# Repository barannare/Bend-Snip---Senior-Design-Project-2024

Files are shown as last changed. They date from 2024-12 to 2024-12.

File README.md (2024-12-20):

# Bend-Snip---Senior-Design-Project-2024
This is the Github Repository for the Tufts University 2024 Mechanical Engineering Senior Design Project - Bend &amp; Snip: The Automated Jumper Wire Cutter. This Project was completed by Elizabeth Abboud, ReAnna Barclay, Emma Gonzalez, and Kaitlin Necakov. The final code and all design materials for this project will be availbale here, as open source.  _Note: The Generative AI, ChatGPT, was used when creating the code for this project to help with syntax and debugging purposes._
AssemblyFinal-3

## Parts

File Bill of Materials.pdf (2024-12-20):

## Bill of Materials

Product: Bend & Snip, Automated Jumper Wire Cutter

Date: Dec 20, 2024

Assembly: Full Machine Assembly

Item # | Part # | Qty | Name | Material | Source | Cost (per unit)
1 | B0D1KQZHKL | 2 | Threaded Rod Lead Screw | 304 Stainless Steel | Amazon | $4.50
2 | B0D1KQZHKL | 2 | Lead Screw Nut | 304 Stainless Steel | Amazon | Included with Item #1
3 | B08ZJ854Z6 | 2 | 5 mm to 8 mm Shaft Coupling | Aluminum Alloy | Amazon | $4.27
4 | B00161GBDW | 2 | Knipex Replacement Blade | Alloy Steel | Amazon | $10.74
5 | B09K1CNP6L | 1 | Boden Dual Gear Extruder | Stainless Steel | Amazon | $47.50
6 | B08ZK8BTNN | 1 | 3D Printer Tube | PTFE | Amazon | $8.99
7 | 1528-1743-ND | 5 | Hook-Up 22 AWG Solid Wire | Copper, PVC | Digikey | $3.19
8 | 1528-1743-ND | 1 | Wooden Dowel Rod | Wood | Digikey | Included with Item #7
9 | 9 | 2, 16.33 g each | Spool Holder Mount | Dual Color PLA | Amazon, Bambu Lab X1C | $0.41

10 | 10 | 1, 38.74 g | Extruder Motor Mount | Dual Color PLA | Amazon, Bambu Lab X1C | $0.98
11 | 11 | 1, 2.77 g | Extruder Motor Knob | Dual Color PLA | Amazon, Bambu Lab X1C | $0.07
12 | 12 | 1, 59.76 g | Bottom Blade Motor Mount | Dual Color PLA | Amazon, Bambu Lab X1C | $1.52
13 | 13 | 1, 12.70 g | Top Blade Mount | Dual Color PLA | Amazon, Bambu Lab X1C | $0.32
14 | 14 | 1, 4.48 g | Lead Screws Holder | Dual Color PLA | Amazon, Bambu Lab X1C | $0.11
15 | 15 | 1, 38.98 g | Bender Motor Mount | Dual Color PLA | Amazon, Bambu Lab X1C | $0.99
16 | 16 | 1, 4.56 g | Bender Arm | Dual Color PLA | Amazon, Bambu Lab X1C | $0.12
17 | 17 | 1, 42.23 g | Slide | Dual Color PLA | Amazon, Bambu Lab X1C | $1.10
18 | 18 | 1, 16.14 g | Bucket | Dual Color PLA | Amazon, Bambu Lab X1C | $0.41
19 | B0046AMGW0 | 1 | Arduino Mega 2560 | Fiberglass, Copper, Semicondu ctors | Amazon | $48.35
20 | 1528-1062-ND | 4 | Nema 17 Stepper Motor | Steel, Copper, Magnets | Digikey | $14.00
21 | B0C5JCF5RS | 3 | L298N Motor Driver | Fiberglass, Copper, Semicondu ctors | Amazon | $2.50

22 | ECPB_M_Multi_ 6P | 2 | Prototype Board Solderable Breadboard | Fiberglass, Copper | Amazon | $1.17
23 | B0B2L66ZFM | 8 | Breadboard Jumper Wires | Copper Clad Aluminum, PVC | Amazon | $0.06
24 | B019K5X53O | 1 | LCD Display Module | Liquid Crystals, Fiberglass, Copper, Semicondu ctors | Amazon | $9.99
25 | B00P7QBGD2 | 1 | Joystick Sensor | Plastic, Fiberglass, Copper, Semicondu ctors | Amazon | $6.99
26 | B072R1H185 | 2 | Arcade Button | Plastic, Fiberglass, Copper, Semicondu ctors | Amazon | $1.36
27 | 27 | 1 | Electronics Mounting Plate | Matte Black Acrylic | Makerstock, Universal VLS 3.60 | $7.75
28 | 28 | 1 | Front Screen Panel | Matte Black Acrylic | Makerstock, Universal VLS 3.60 | $7.75
29 | 29 | 1 | Side Port Panel | Matte Black Acrylic | Makerstock, Universal VLS 3.60 | $7.75
30 | 30 | 1 | Divider Panel | Matte Black Acrylic | Makerstock, Universal VLS 3.60 | $7.75
31 | 31 | 1 | Back Vent Panel | Matte Black Acrylic | Makerstock, Universal VLS 3.60 | $7.75

32 | 32 | 2 | Front/Back Enclosure Panel | Clear Acrylic | Makerstock, Universal VLS 3.60 | $4.48
33 | 33 | 2 | Sides Enclosure Panel | Clear Acrylic | Makerstock, Universal VLS 3.60 | $4.48
34 | 34 | 1 | Top Enclosure Panel | Clear Acrylic | Makerstock, Universal VLS 3.60 | $8.95
35 | B0BSDNPTL8 | 4 | Acrylic Corner Brackets | Clear Acrylic | Amazon | $1.28
36 | B0BSDNPTL8 | 12 | Acrylic Corner Bracket Bolts | Clear Acrylic | Amazon | Included with Item #35
37 | B0BSDNPTL8 | 12 | Acrylic Corner Bracket Nuts | Clear Acrylic | Amazon | Included with Item #35
38 | 38 | 4 | Aluminum Extrusion 315.6 mm | Silver Anodized Aluminum | McMaster-Carr | $2.84
39 | 39 | 4 | Aluminum Extrusion 177.8 mm | Silver Anodized Aluminum | McMaster-Carr | $2.84
40 | 40 | 4 | Aluminum Extrusion 101.6 mm | Silver Anodized Aluminum | McMaster-Carr | $2.84
41 | B0855V2JV3 | 20 | Aluminum Extrusion Corner Bracket | Aluminum | Amazon | $0.95
43 | 3136N409 | 55 | M5 x 0.8 mm 10 mm Long Socket Button Head Bolt | Zinc-Plated Steel | McMaster-Carr | $0.77
44 | 3136N409 | 55 | M5 x 0.8 mm Aluminum Extrusion Nut | Zinc-Plated Steel | McMaster-Carr | $0.77
45 | 91290A124 | 8 | M3 x 0.5 mm 22 mm Long | Black Oxide Class | McMaster-Carr | $0.13

| | | Socket Head Cap Bolt | 12.9 Alloy Steel
46 | 91290A119 | 2 | M3 x 0.5 mm 14 mm Long Socket Head CapBolt | Black Oxide Class 12.9 Alloy Steel | McMaster-Carr | $0.15
47 | 91290A115 | 44 | M3 x 0.5 mm 10 mm Long Socket Head Cap Bolt | Black Oxide Class 12.9 Alloy Steel | McMaster-Carr | $0.13
48 | 91290A109 | 12 | M3 x 0.5 mm 4 mm Long Socket HeadCap Bolt | Black Oxide Class 12.9 Alloy Steel | McMaster-Carr | $0.13
49 | 90591A250 | 66 | M3 x 0.5 mm Hex Nut | Zinc-Plated Steel | McMaster-Carr | $0.03
50 | 91290A049 | 4 | M2 x 0.4 mm 20 mm Long Socket Head Bolt | Black Oxide Class 12.9 Alloy Steel | McMaster-Carr | $0.15
51 | 90128A181 | 4 | M2 x 0.4 mm 10 mm Long Socket Head Cap Bolt | Zinc-Plated Class 12.9 Alloy Steel | McMaster-Carr | $0.13
52 | 90128A179 | 9 | M2 x 0.4 mm 8 mm Long Socket Head Cap Bolt | Zinc-Plated Class 12.9 Alloy Steel | McMaster-Carr | $0.13
53 | 09591A265 | 17 | M2 Hex Nut | Zinc-Plated Steel | McMaster-Carr | $0.02
54 | 54 | 1 | Assembly Mounting Plate | Matte Black Acrylic | Makerstock, Universal VLS 3.60 | $7.75
55 | B07DC5VFZ7 | 2 | 10 mm LED | Copper, Semicondu ctors | Amazon | $0.40
56 | B0C8141GB1 | 2 | L Bracket | Stainless Steel | Amazon | $0.15

Team Member | Prepared by: Kaitlin Necakov
Team Member | Checked by: ReAnna Barclay
Team Member | Approved by: Elizabeth Abboud

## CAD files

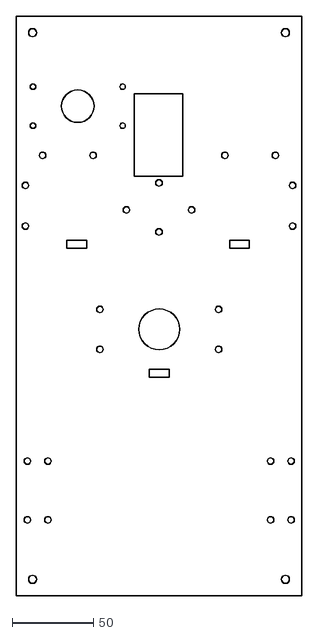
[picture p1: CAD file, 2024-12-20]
DXF Files/Assembly Mounting Plate.dxf
175.3 x 355.6

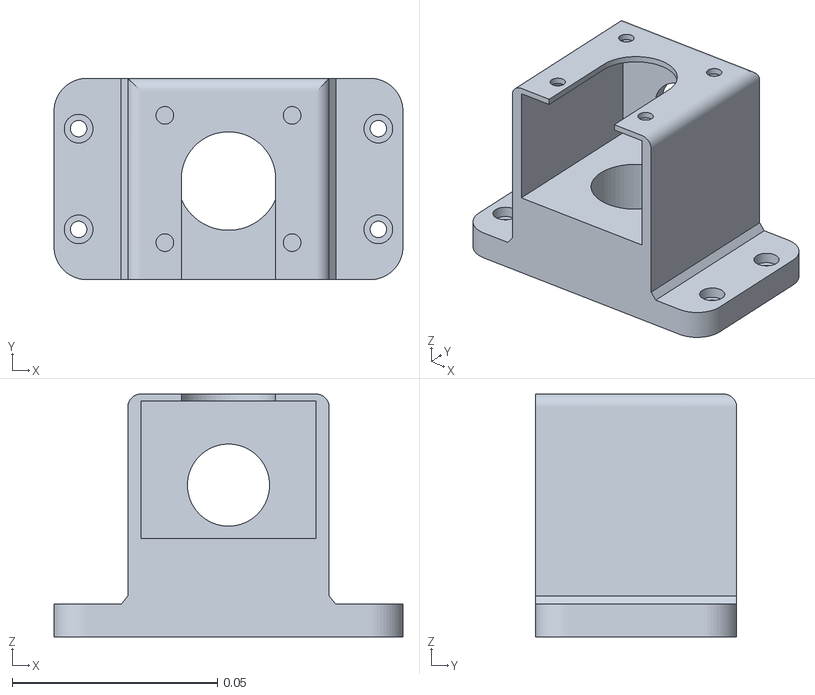
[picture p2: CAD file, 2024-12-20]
3D Print STL Files/Extruder Motor Mount.stl
0.085 x 0.049 x 0.0592

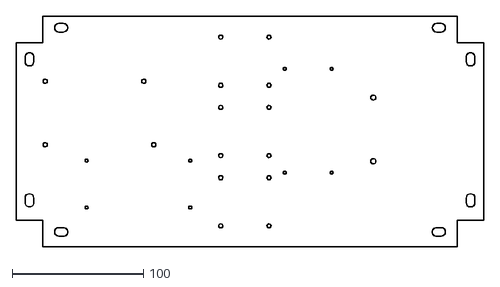
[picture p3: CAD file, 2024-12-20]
DXF Files/Electronics Mounting Plate.dxf
355.6 x 175.3

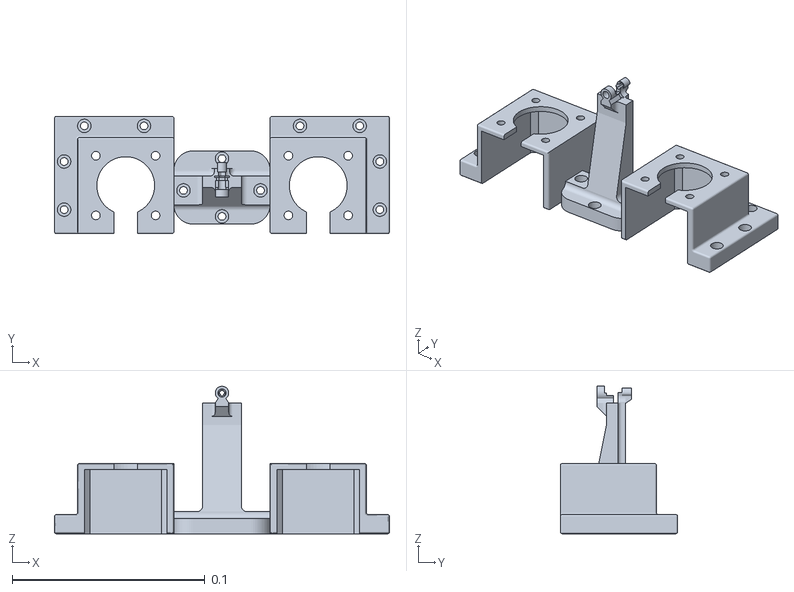
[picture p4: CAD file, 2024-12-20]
3D Print STL Files/Bottom Blade Motor Mount.stl
0.174 x 0.061 x 0.0766

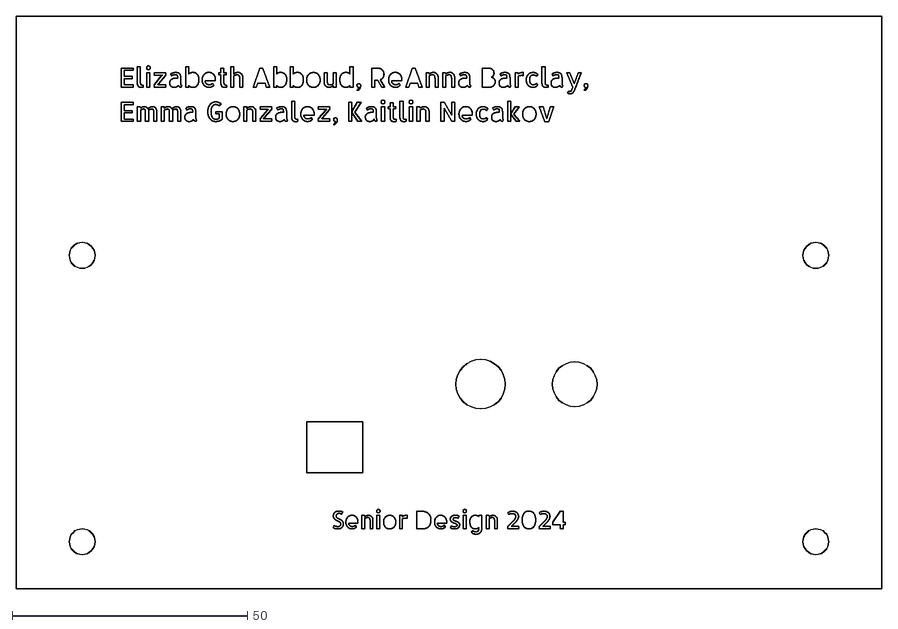
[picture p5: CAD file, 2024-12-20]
DXF Files/Side Port Panel.dxf
183.8 x 121.6

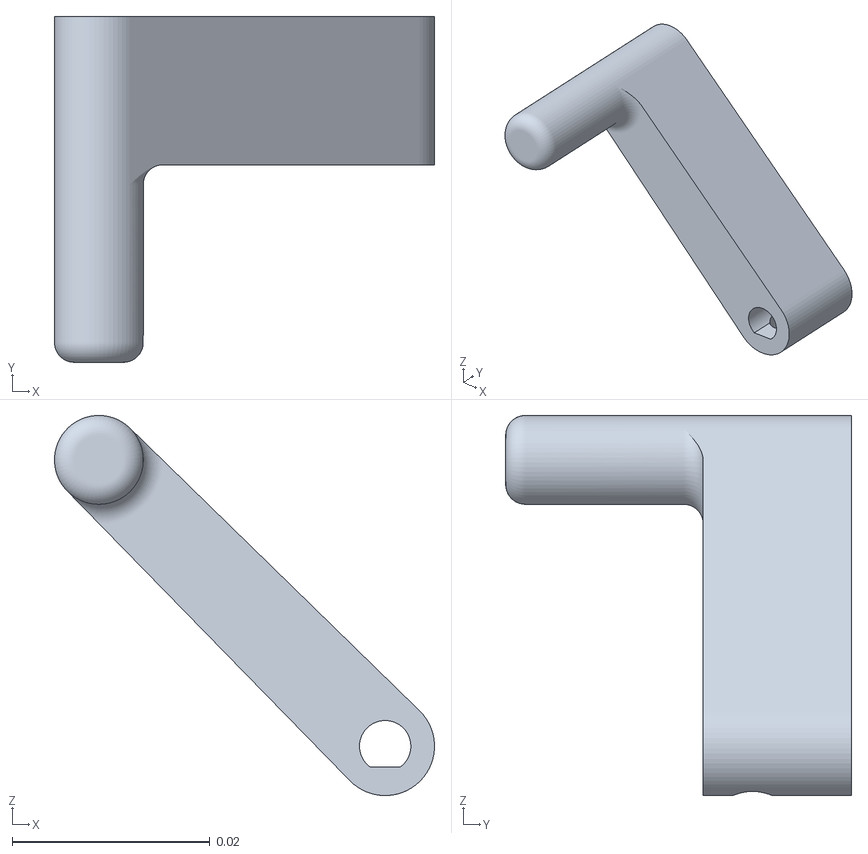
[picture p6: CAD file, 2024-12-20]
3D Print STL Files/Bender Arm.stl
0.0385 x 0.035 x 0.0385

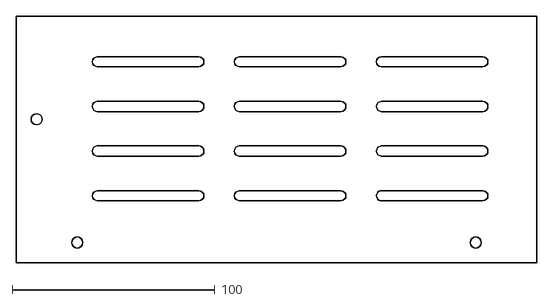
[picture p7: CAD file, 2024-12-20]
DXF Files/Back Vent Wall.dxf
256.5 x 121.6

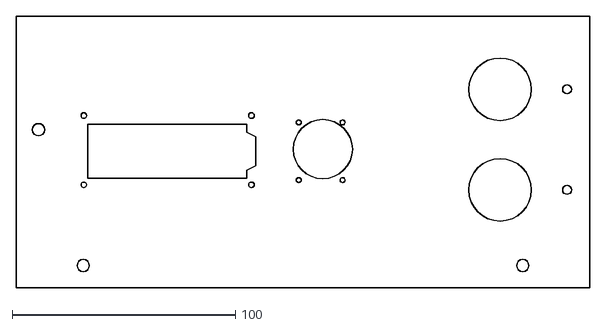
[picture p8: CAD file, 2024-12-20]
DXF Files/Front Screen Panel.dxf
256.7 x 121.6

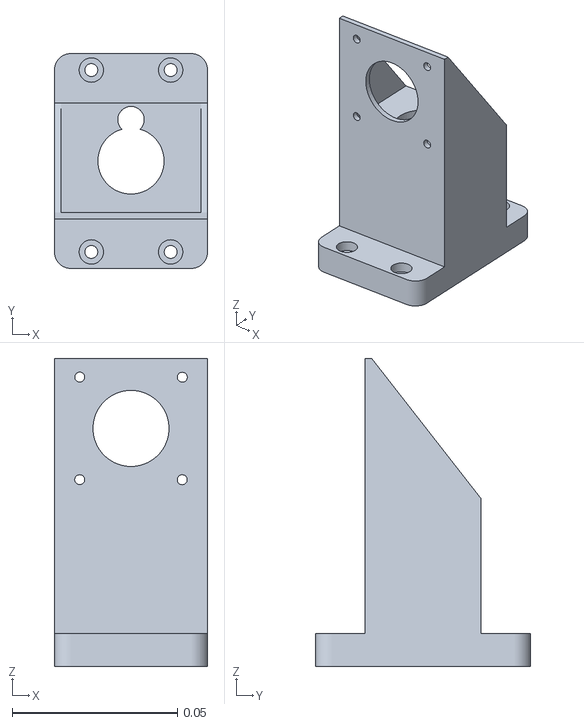
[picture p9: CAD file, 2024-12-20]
3D Print STL Files/Bender Motor Mount.stl
0.0463 x 0.065 x 0.0931

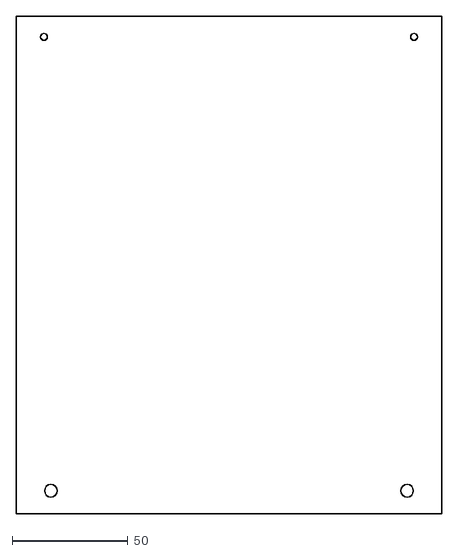
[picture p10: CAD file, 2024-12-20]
DXF Files/Sides Enclosure Panel.dxf
183.8 x 215.0

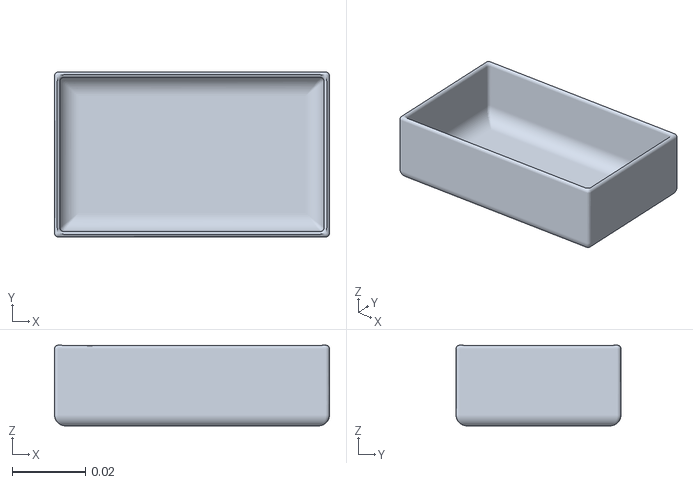
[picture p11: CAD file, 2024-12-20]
3D Print STL Files/Bucket.stl
0.075 x 0.045 x 0.022

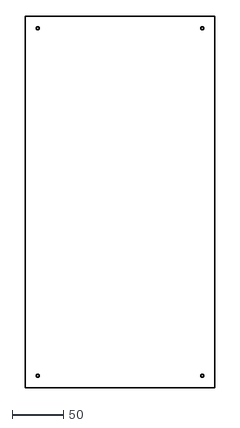
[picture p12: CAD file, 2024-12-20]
DXF Files/Top Enclosure Panel.dxf
183.8 x 361.6

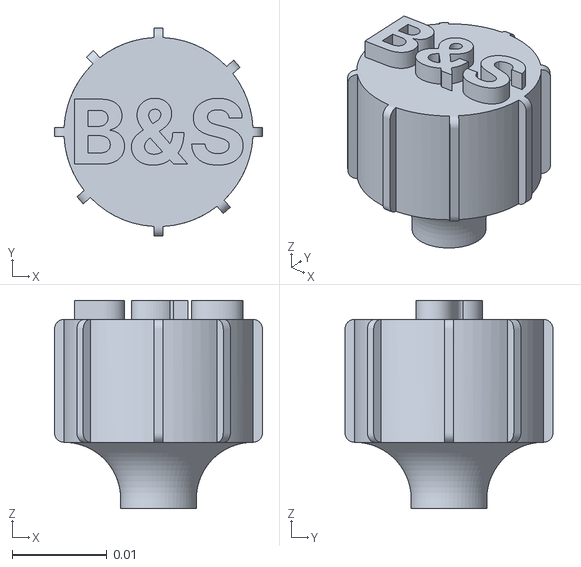
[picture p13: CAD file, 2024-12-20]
3D Print STL Files/Extruder Motor Knob.stl
0.022 x 0.022 x 0.022

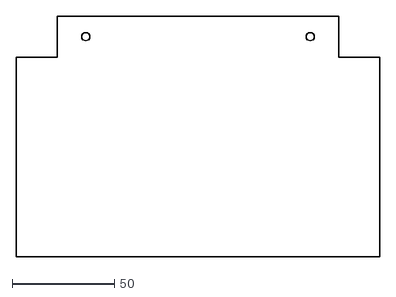
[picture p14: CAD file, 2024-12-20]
DXF Files/Divider Panel.dxf
177.8 x 117.6

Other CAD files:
3D Print STL Files/Top Blade Mount.stl
DXF Files/Front-Back Enclosure Panel.dxf
3D Print STL Files/Spool Holder Mount.stl
3D Print STL Files/Slide.stl
3D Print STL Files/Lead Screws Holder.stl

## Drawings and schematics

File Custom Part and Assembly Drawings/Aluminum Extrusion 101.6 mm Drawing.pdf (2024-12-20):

2
1

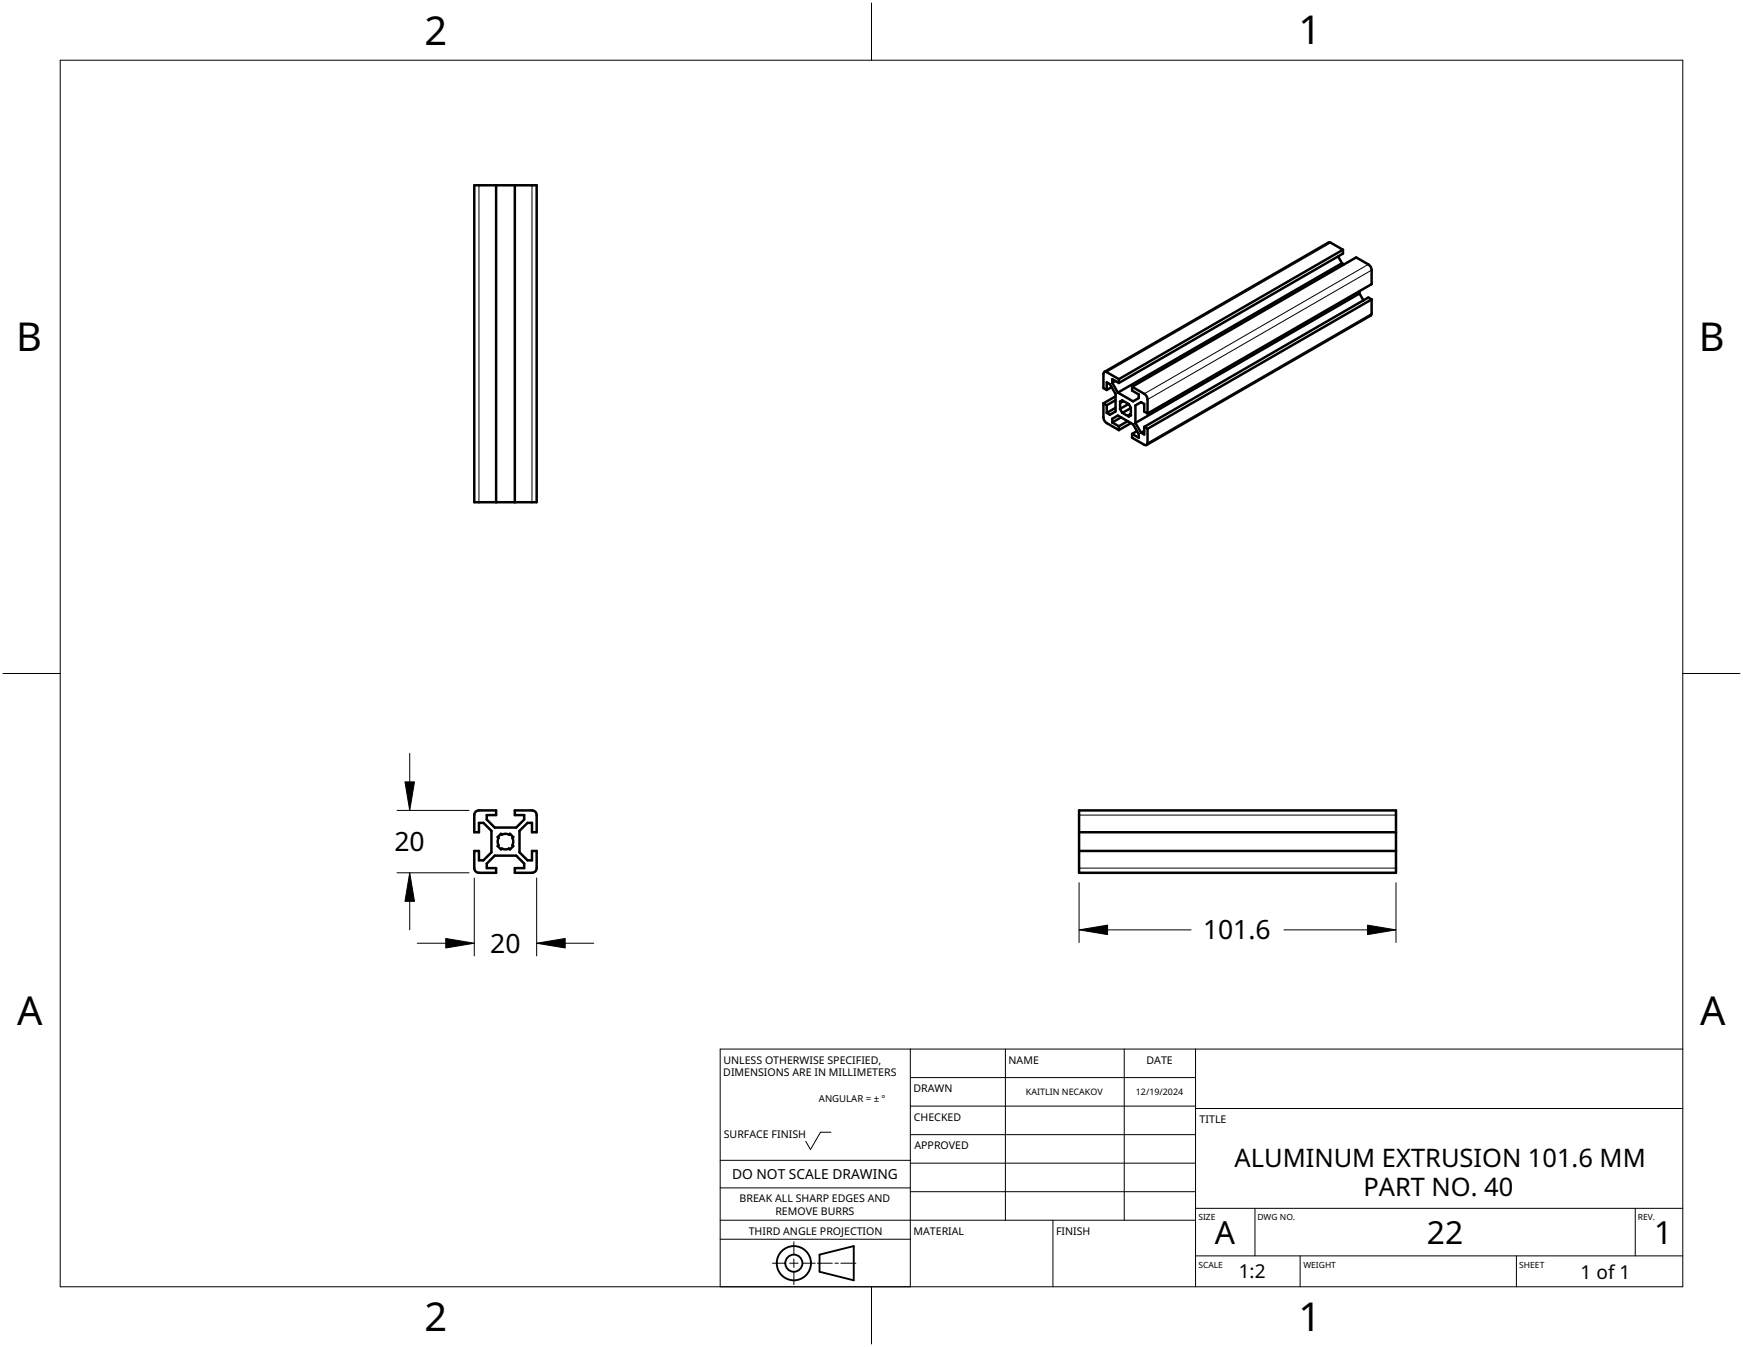
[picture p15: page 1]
MATERIAL; FINISH

UNLESS OTHERWISE SPECIFIED, DIMENSIONS ARE IN MILLIMETERS ANGULAR = ± ° SURFACE FINISH | | NAME | DATE

DRAWN | KAITLIN NECAKOV | 12/19/2024

CHECKED | | | TITLE ALUMINUM EXTRUSION 101.6 MM PART NO. 40

APPROVED

DO NOT SCALE DRAWING

BREAK ALL SHARP EDGES AND

REMOVE BURRS
THIRD ANGLE PROJECTION

SIZE A | DWG NO. 22 | REV. 1

SCALE 1:2 | WEIGHT | SHEET 1 of 1

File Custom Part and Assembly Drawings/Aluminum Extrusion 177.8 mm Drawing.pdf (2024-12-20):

2
1

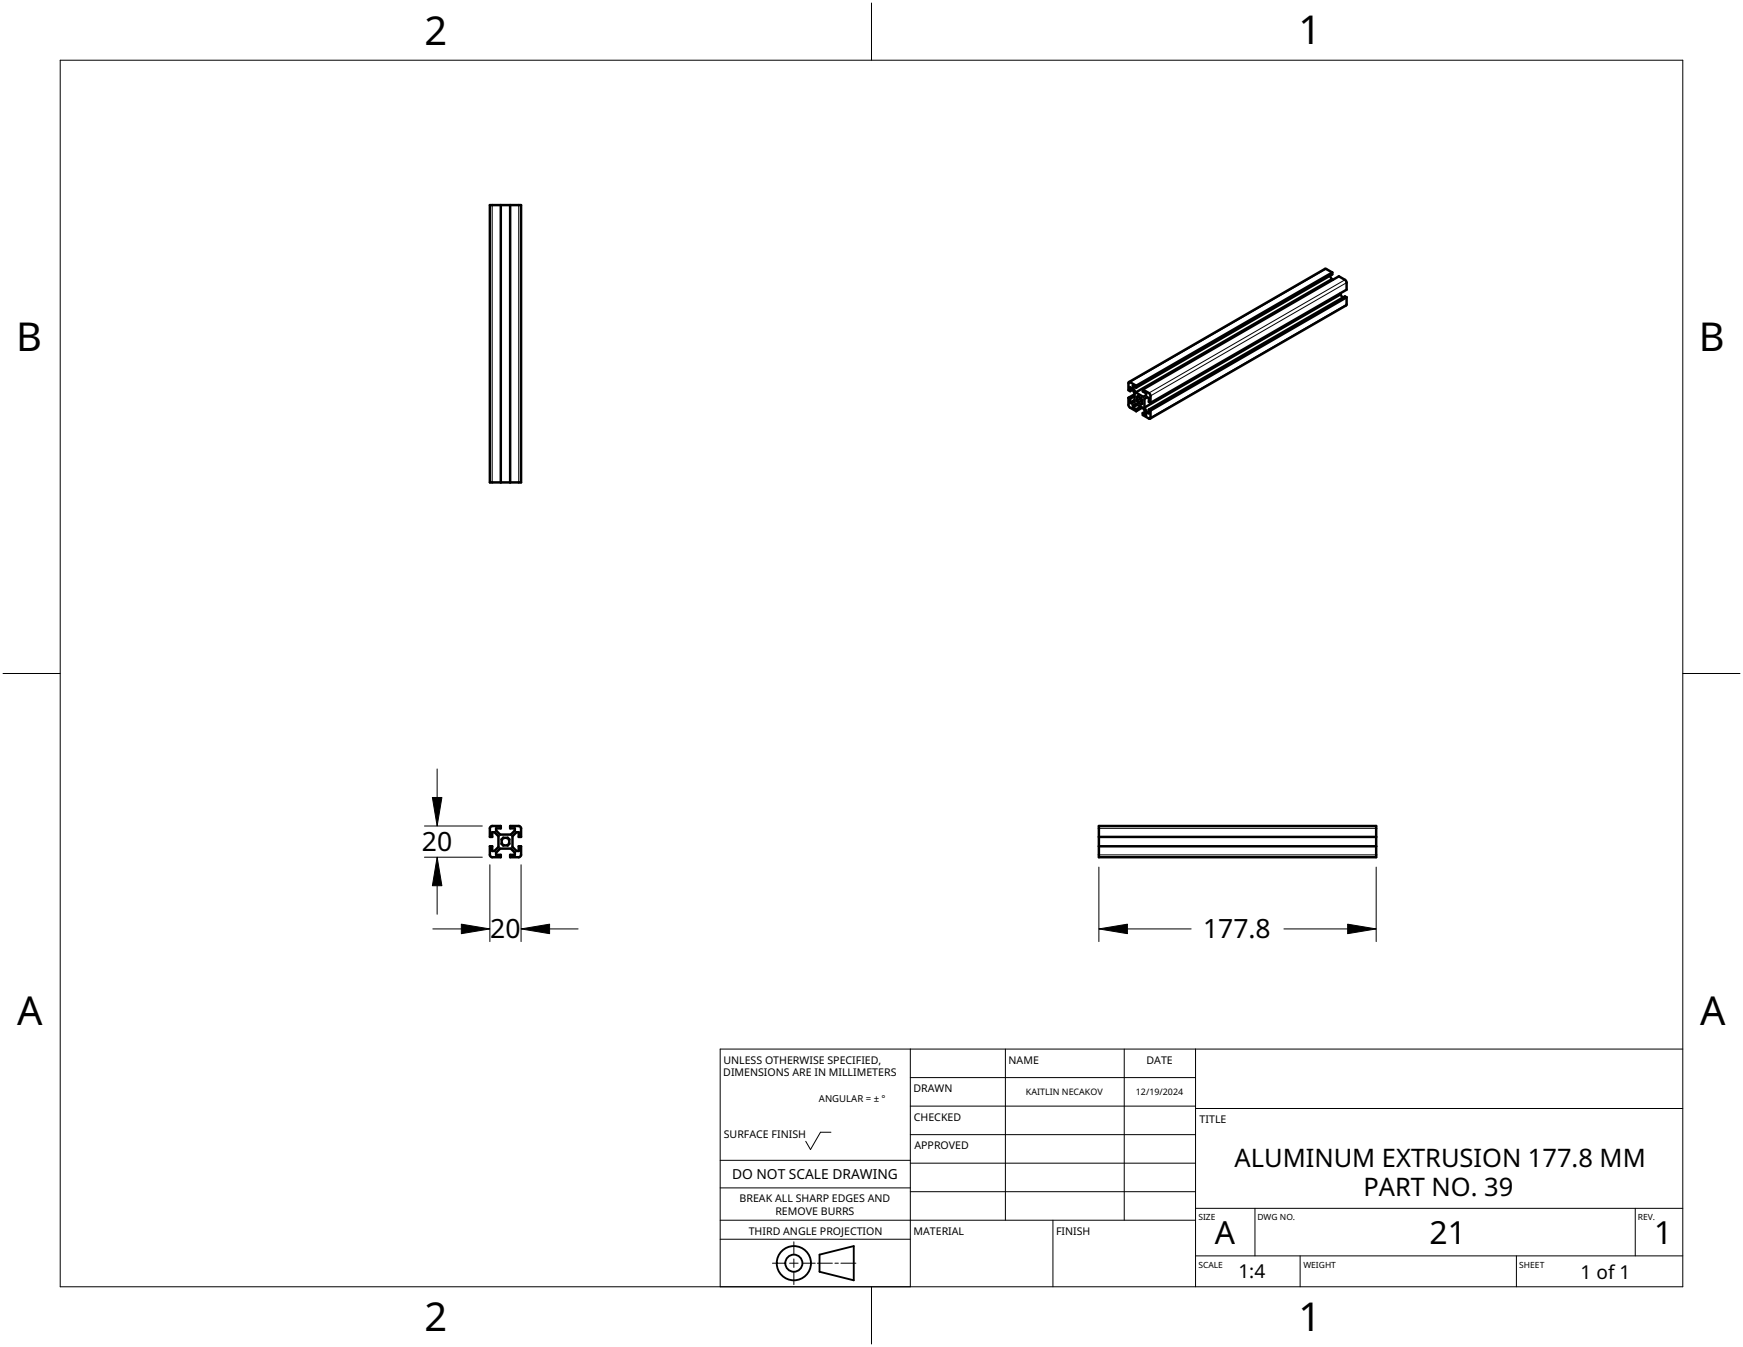
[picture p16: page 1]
MATERIAL; FINISH

UNLESS OTHERWISE SPECIFIED, DIMENSIONS ARE IN MILLIMETERS ANGULAR = ± ° SURFACE FINISH | | NAME | DATE

DRAWN | KAITLIN NECAKOV | 12/19/2024

CHECKED | | | TITLE ALUMINUM EXTRUSION 177.8 MM PART NO. 39

APPROVED

DO NOT SCALE DRAWING

BREAK ALL SHARP EDGES AND

REMOVE BURRS
THIRD ANGLE PROJECTION

SIZE A | DWG NO. 21 | REV. 1

SCALE 1:4 | WEIGHT | SHEET 1 of 1

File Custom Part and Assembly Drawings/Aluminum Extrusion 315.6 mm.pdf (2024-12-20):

2
1

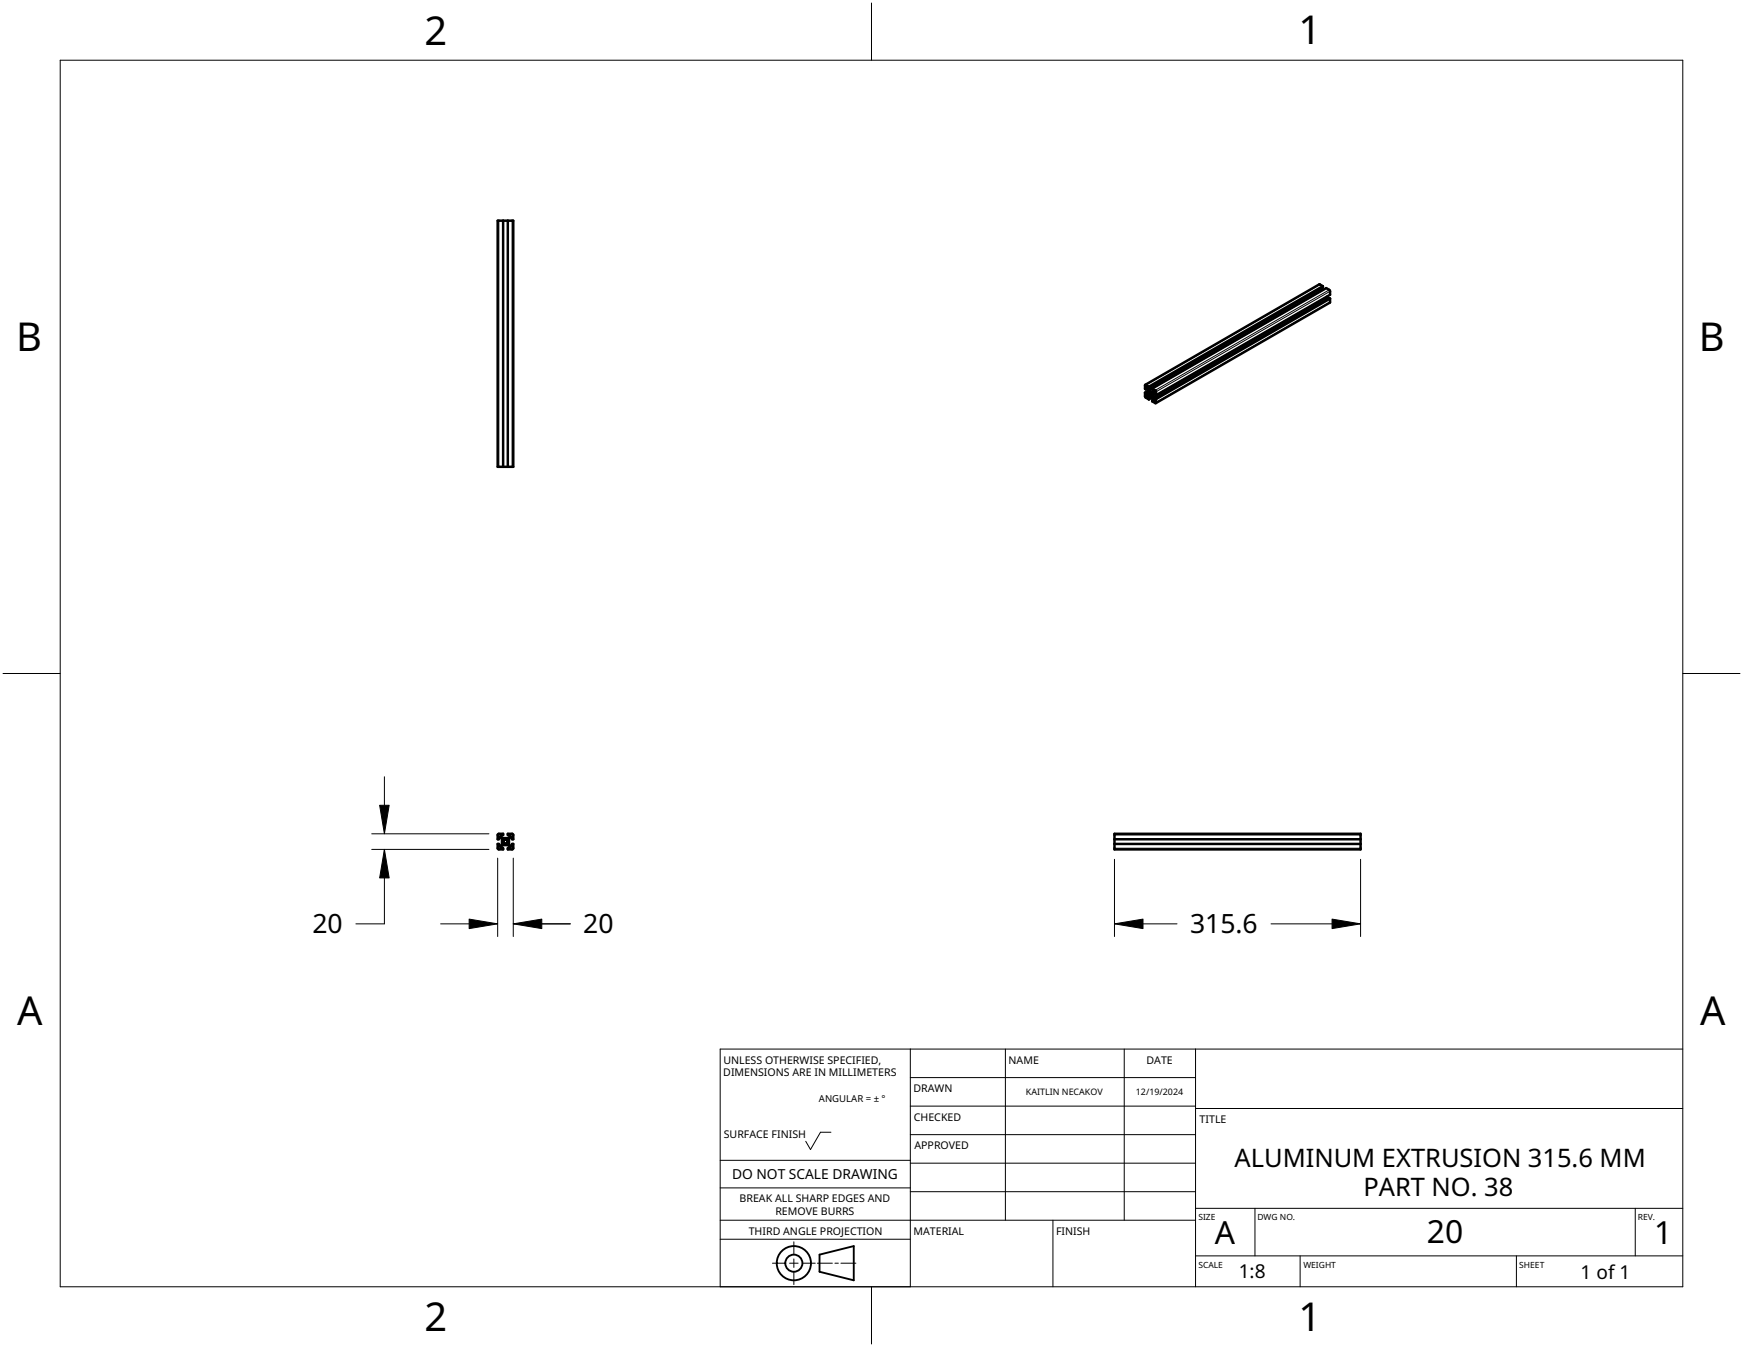
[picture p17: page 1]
MATERIAL; FINISH

UNLESS OTHERWISE SPECIFIED, DIMENSIONS ARE IN MILLIMETERS ANGULAR = ± ° SURFACE FINISH | | NAME | DATE

DRAWN | KAITLIN NECAKOV | 12/19/2024

CHECKED | | | TITLE ALUMINUM EXTRUSION 315.6 MM PART NO. 38

APPROVED

DO NOT SCALE DRAWING

BREAK ALL SHARP EDGES AND

REMOVE BURRS
THIRD ANGLE PROJECTION

SIZE A | DWG NO. 20 | REV. 1

SCALE 1:8 | WEIGHT | SHEET 1 of 1

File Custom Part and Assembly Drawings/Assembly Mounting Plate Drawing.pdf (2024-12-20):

2
1

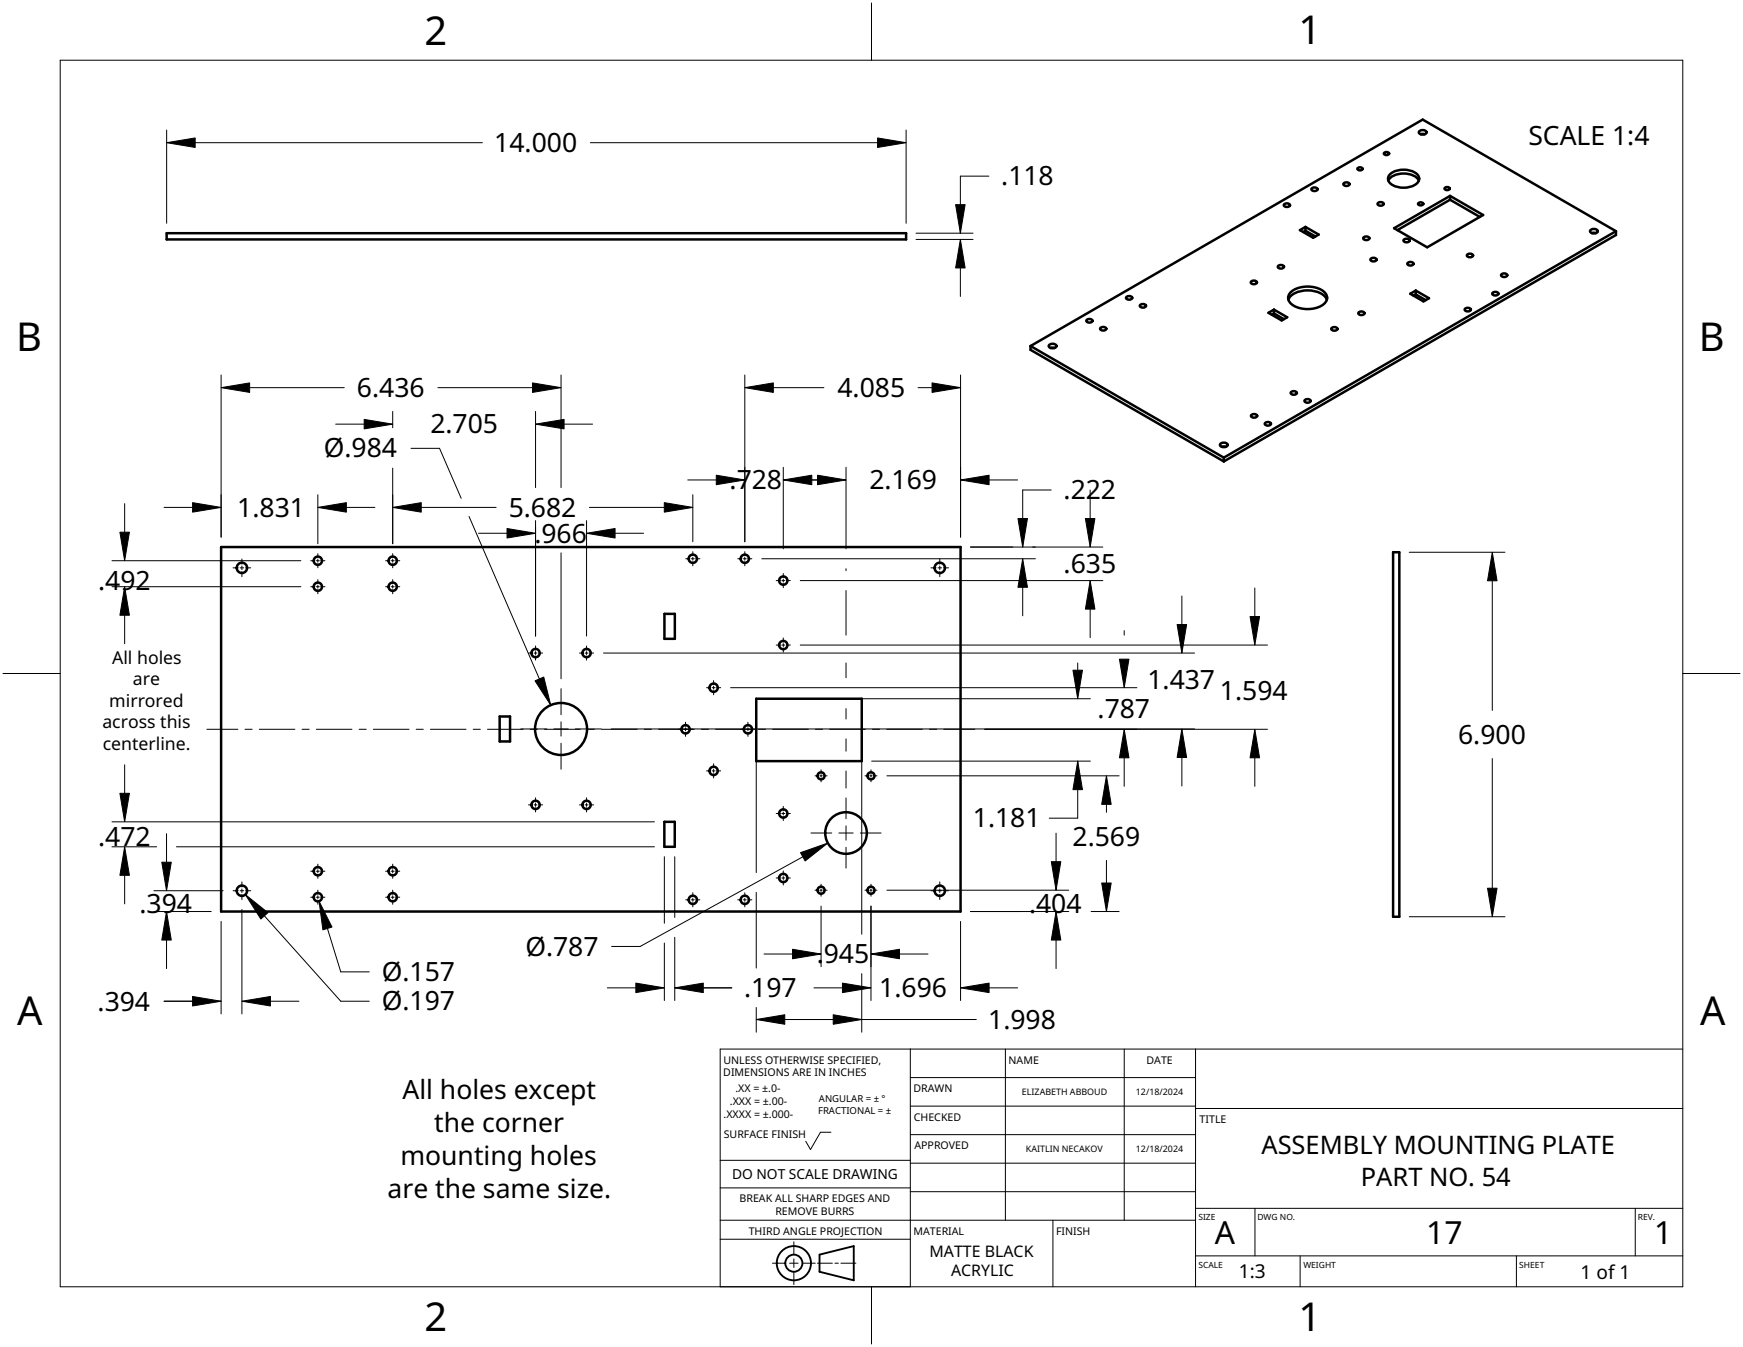
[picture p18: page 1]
MATERIAL MATTE BLACK ACRYLIC; FINISH; SCALE 1:4; All holes; are mirrored across this centerline.

UNLESS OTHERWISE SPECIFIED, DIMENSIONS ARE IN INCHES .XX = ±.0-.XXX = ±.00-ANGULAR = ± ° .XXXX = ±.000-FRACTIONAL = ± SURFACE FINISH | | NAME | DATE

All holes except
the corner
mounting holes
are the same size.

DRAWN | ELIZABETH ABBOUD | 12/18/2024

CHECKED | | | TITLE ASSEMBLY MOUNTING PLATE PART NO. 54

APPROVED | KAITLIN NECAKOV | 12/18/2024

DO NOT SCALE DRAWING

BREAK ALL SHARP EDGES AND

REMOVE BURRS
THIRD ANGLE PROJECTION

SIZE A | DWG NO. 17 | REV. 1

SCALE 1:3 | WEIGHT | SHEET 1 of 1

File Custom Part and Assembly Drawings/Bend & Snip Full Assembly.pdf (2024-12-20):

2
1

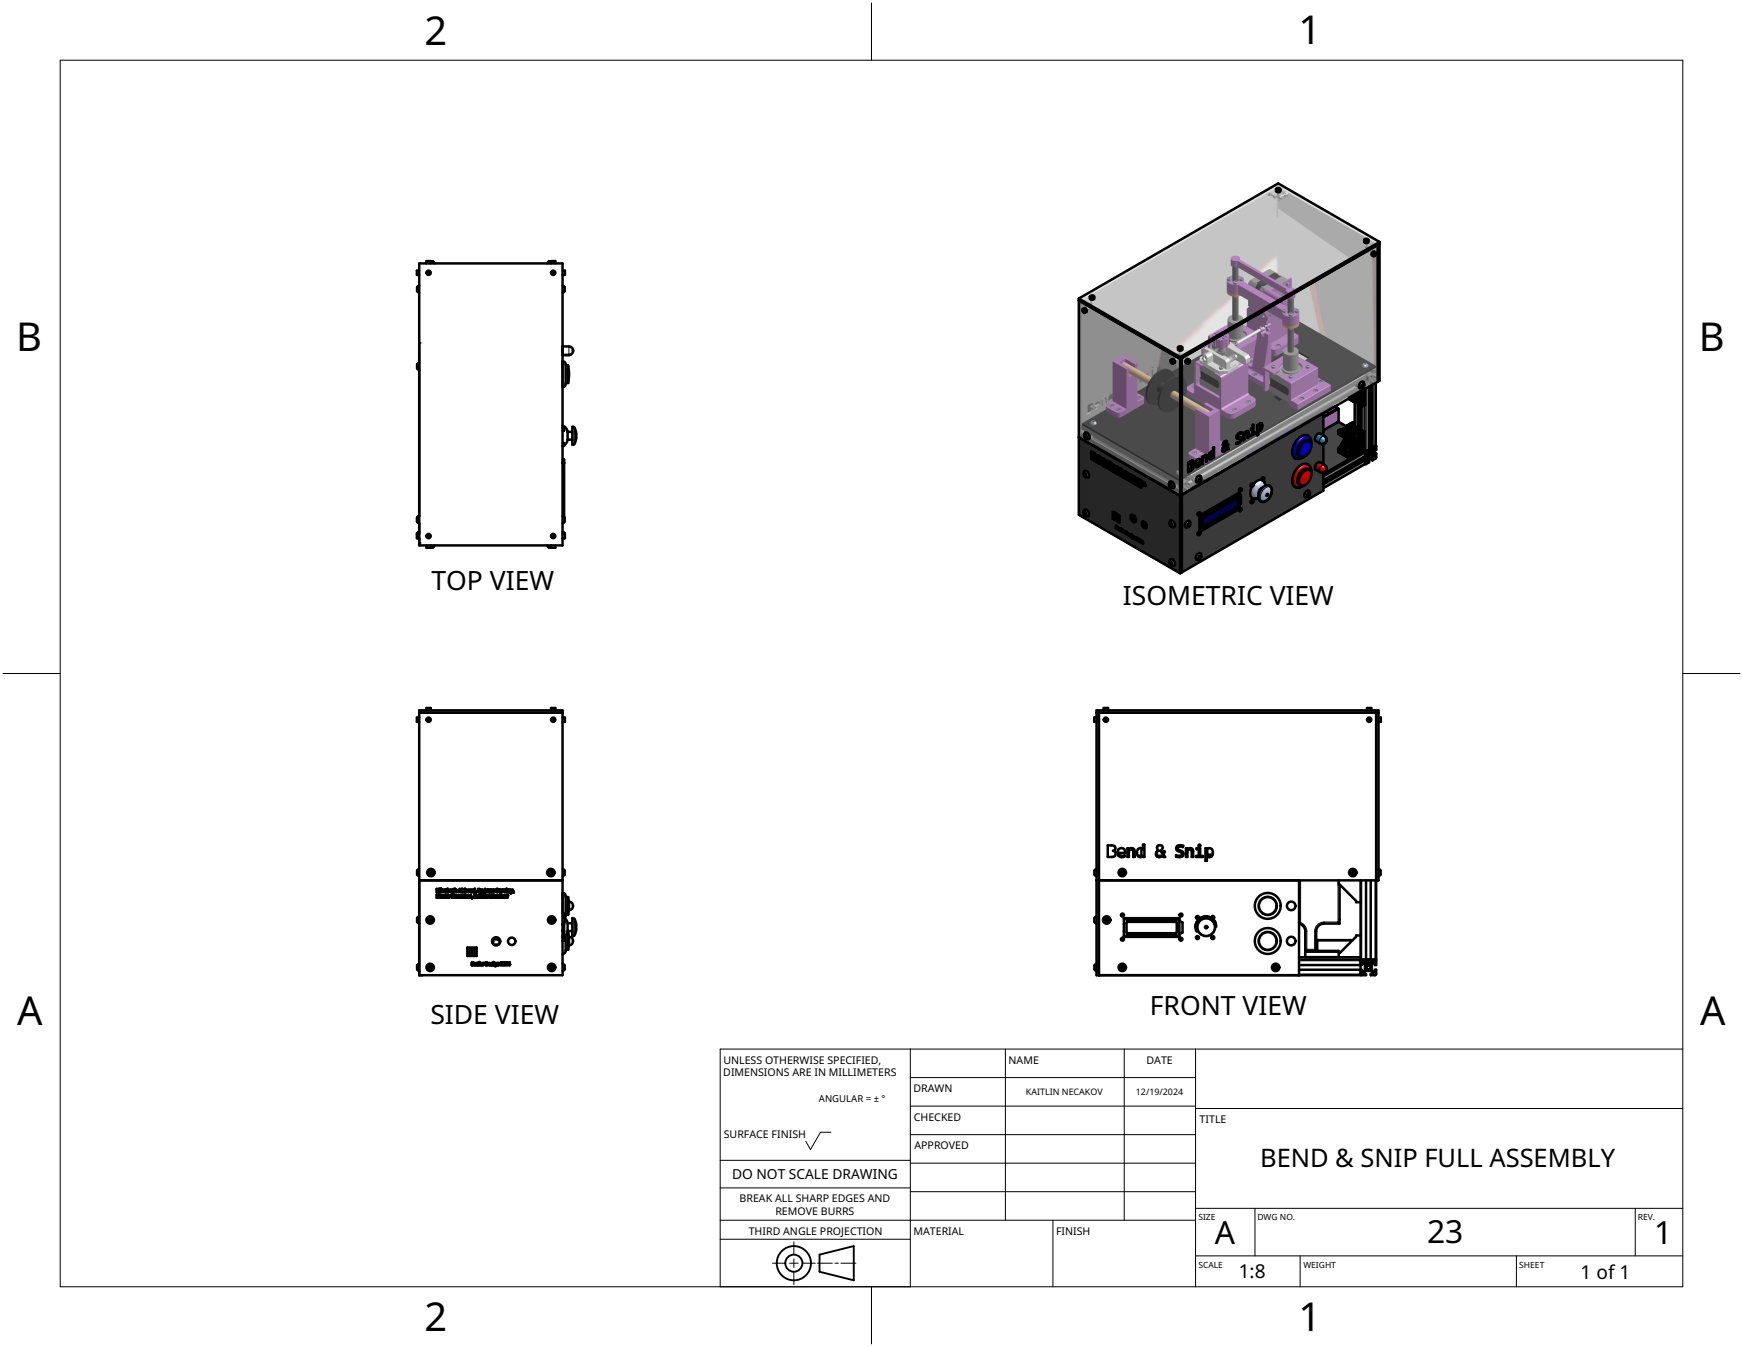
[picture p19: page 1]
MATERIAL; FINISH; ISOMETRIC VIEW; SIDE VIEW; FRONT VIEW; TOP VIEW

UNLESS OTHERWISE SPECIFIED, DIMENSIONS ARE IN MILLIMETERS ANGULAR = ± ° SURFACE FINISH | | NAME | DATE

DRAWN | KAITLIN NECAKOV | 12/19/2024

CHECKED | | | TITLE BEND & SNIP FULL ASSEMBLY

APPROVED

DO NOT SCALE DRAWING

BREAK ALL SHARP EDGES AND

REMOVE BURRS
THIRD ANGLE PROJECTION

SIZE A | DWG NO. 23 | REV. 1

SCALE 1:8 | WEIGHT | SHEET 1 of 1

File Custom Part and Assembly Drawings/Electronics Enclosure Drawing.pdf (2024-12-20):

2
1

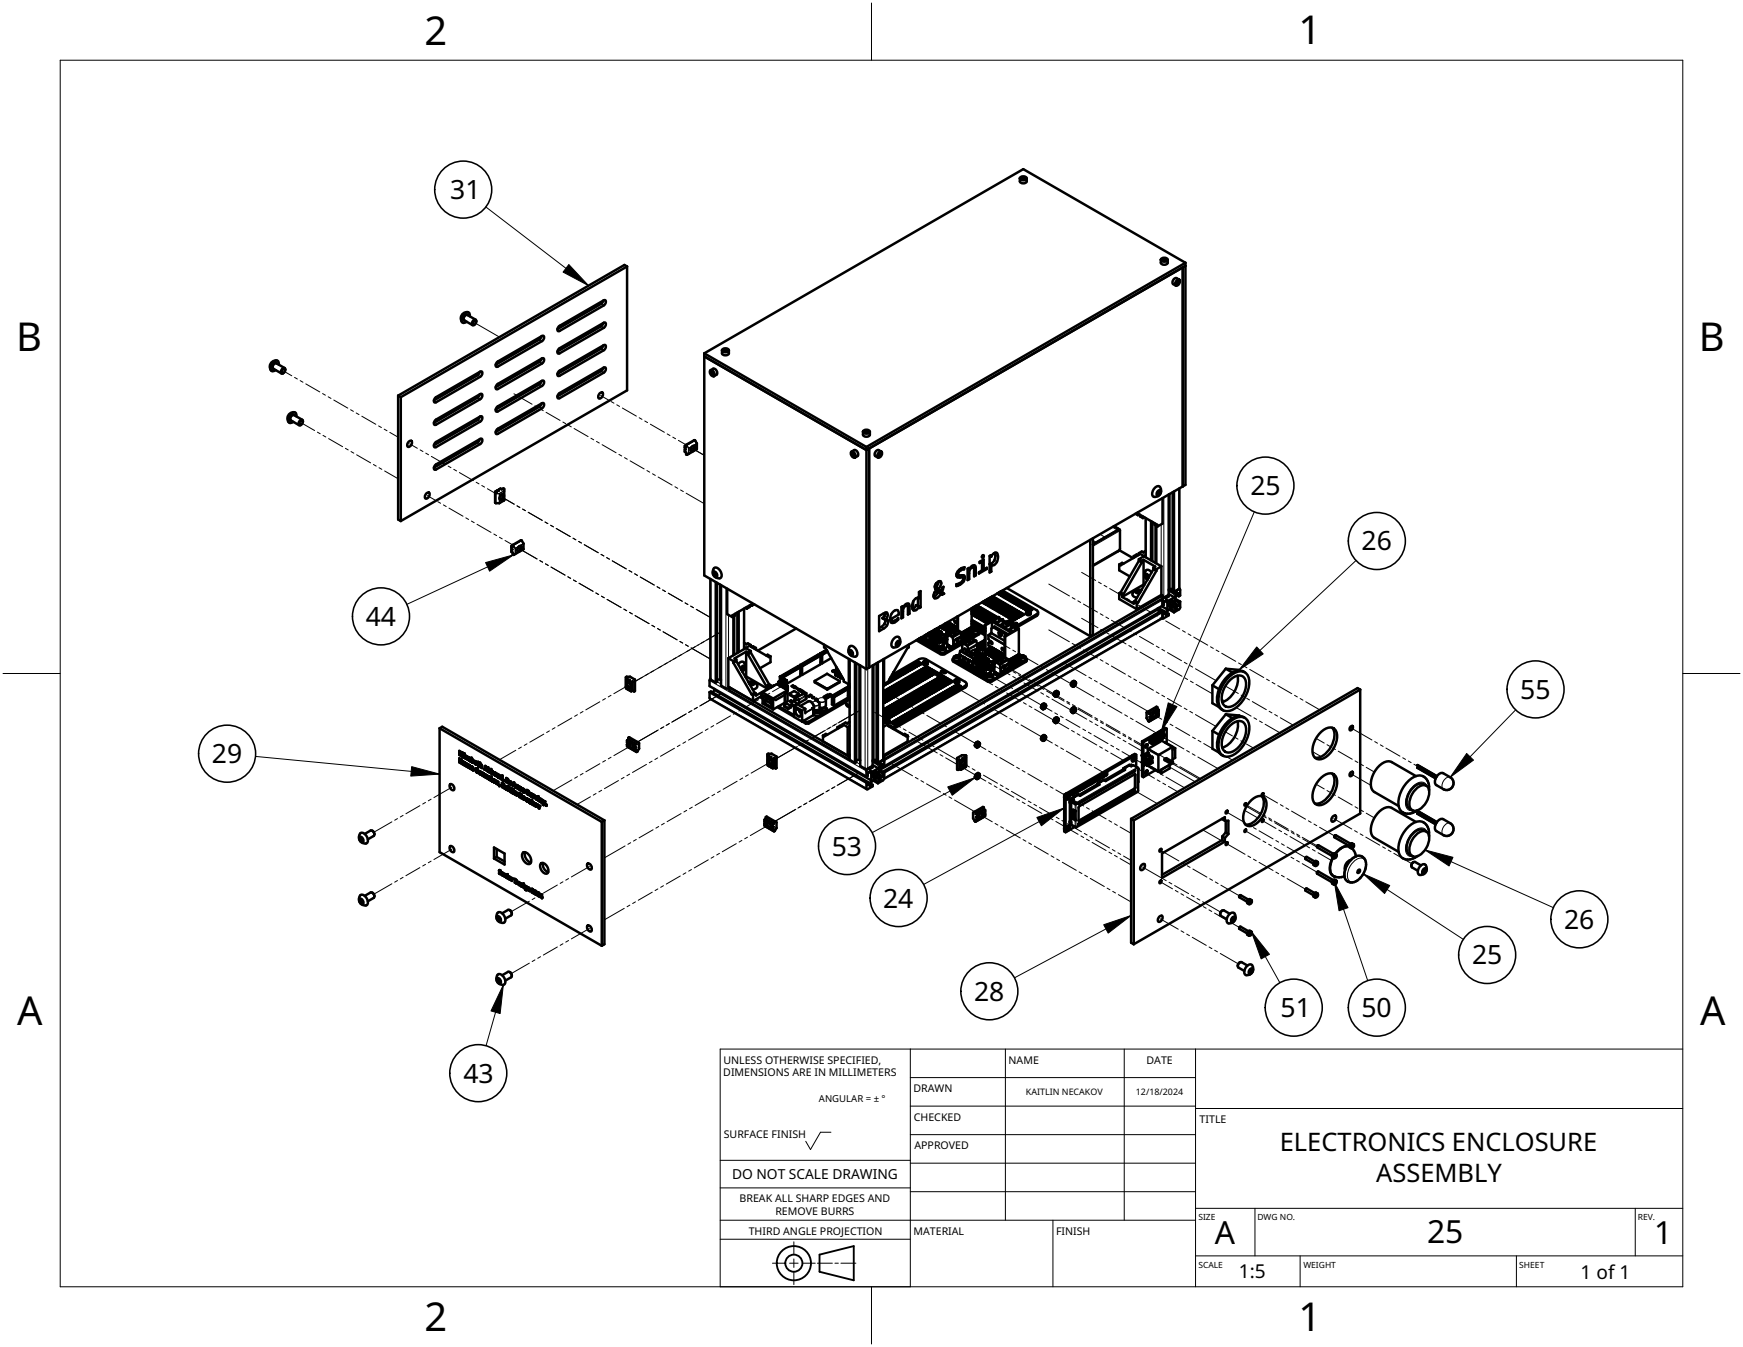
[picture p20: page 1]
ANGULAR = ± °; SURFACE FINISH; NAME; DATE; DRAWN; KAITLIN NECAKOV; CHECKED; APPROVED; MATERIAL; FINISH; TITLE; ELECTRONICS ENCLOSURE ASSEMBLY; SIZE A; DWG NO.; REV. 1; SCALE; WEIGHT; SHEET

UNLESS OTHERWISE SPECIFIED,
DIMENSIONS ARE IN MILLIMETERS

DO NOT SCALE DRAWING

BREAK ALL SHARP EDGES AND

REMOVE BURRS
THIRD ANGLE PROJECTION

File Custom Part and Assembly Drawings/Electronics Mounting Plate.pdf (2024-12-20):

2
1

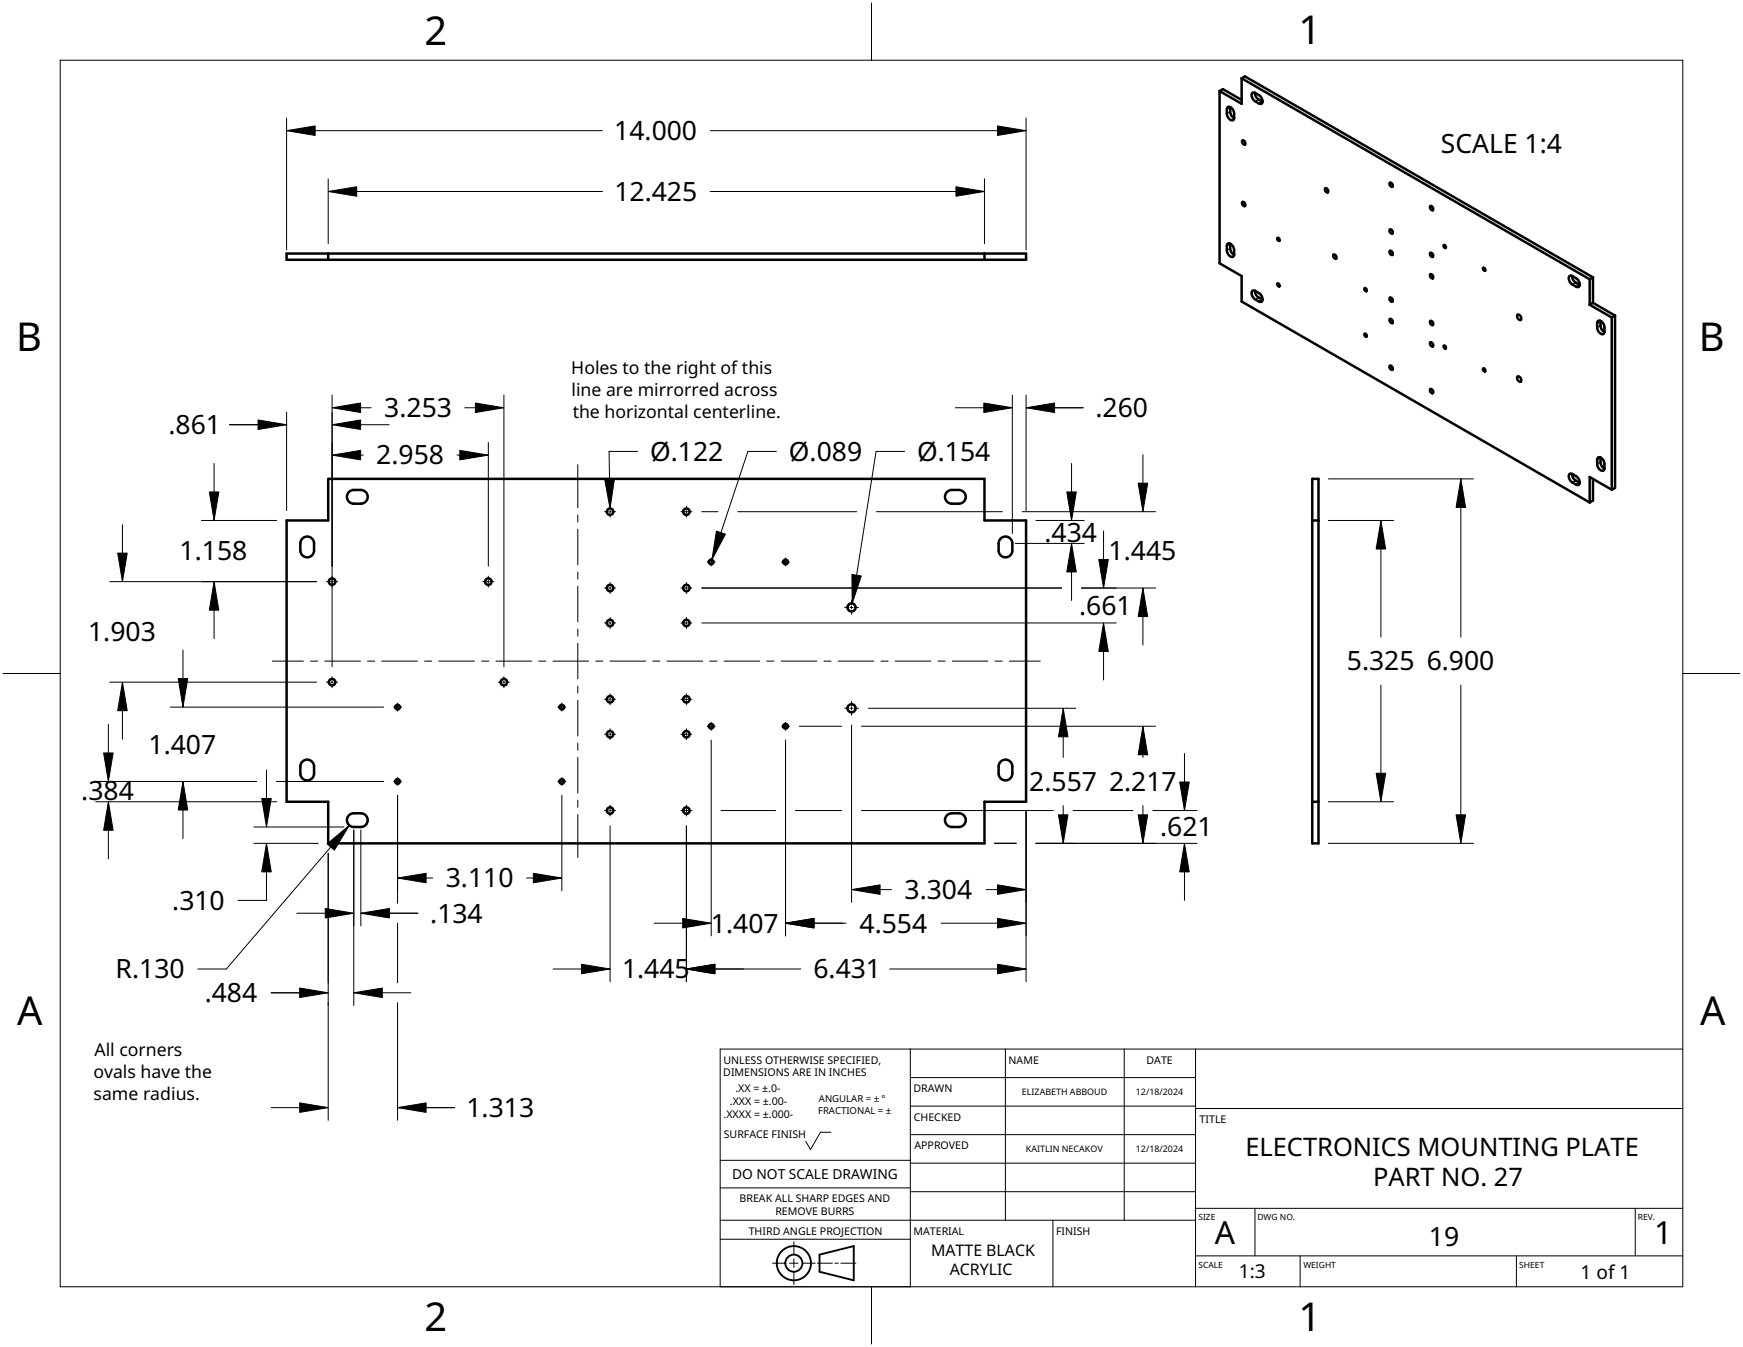
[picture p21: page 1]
MATERIAL MATTE BLACK ACRYLIC; FINISH; SCALE 1:4

Holes to the right of this
line are mirrorred across
the horizontal centerline.

All corners
ovals have the
same radius.

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

DRAWN | ELIZABETH ABBOUD | 12/18/2024

CHECKED | | | TITLE ELECTRONICS MOUNTING PLATE PART NO. 27

APPROVED | KAITLIN NECAKOV | 12/18/2024

DO NOT SCALE DRAWING

BREAK ALL SHARP EDGES AND

REMOVE BURRS
THIRD ANGLE PROJECTION

SIZE A | DWG NO. 19 | REV. 1

SCALE 1:3 | WEIGHT | SHEET 1 of 1

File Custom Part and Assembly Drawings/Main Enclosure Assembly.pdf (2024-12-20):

2
1

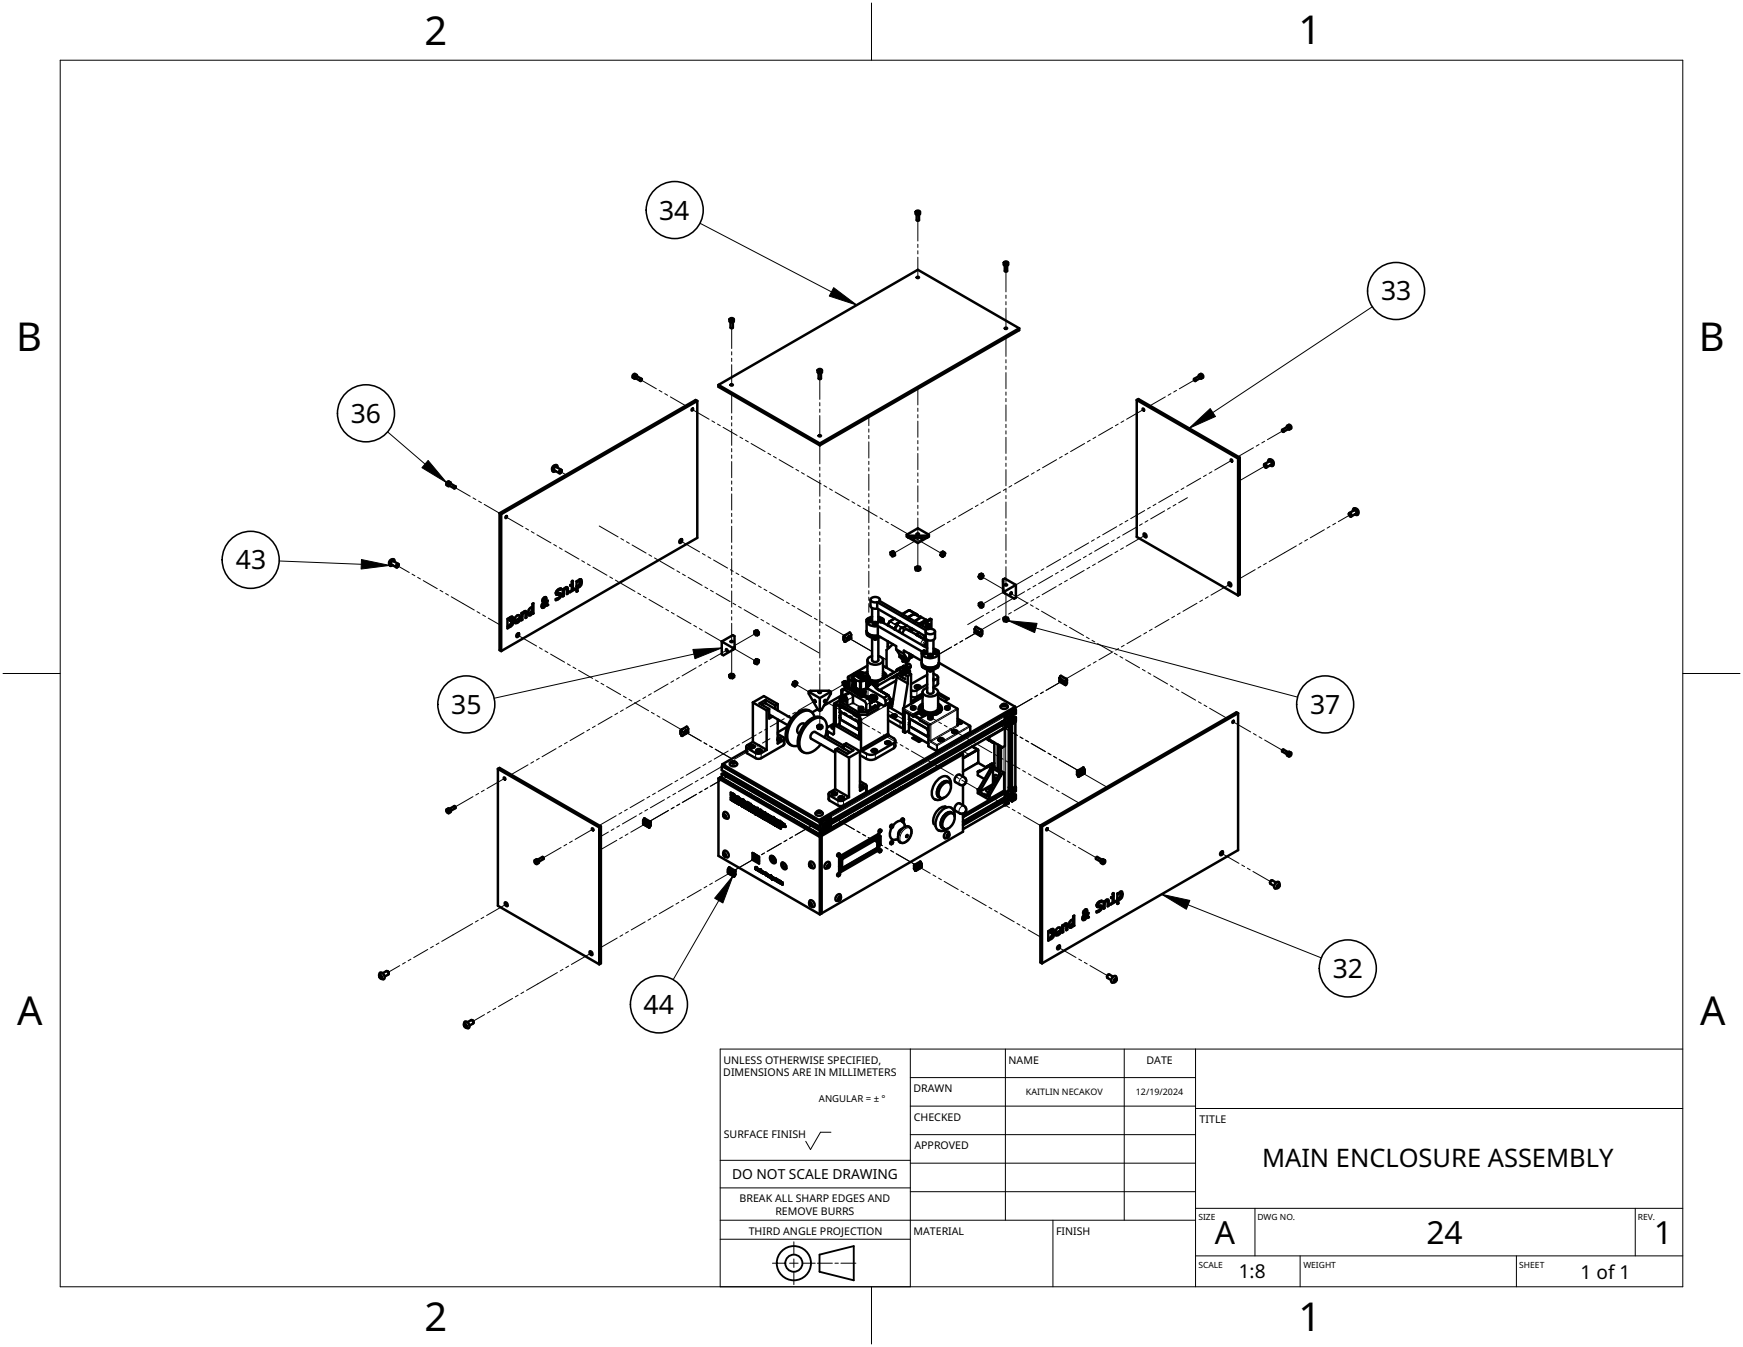
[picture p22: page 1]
ANGULAR = ± °; SURFACE FINISH; NAME; DATE; DRAWN; KAITLIN NECAKOV; CHECKED; APPROVED; MATERIAL; FINISH; SIZE A; DWG NO.; REV. 1; SCALE; WEIGHT; SHEET

UNLESS OTHERWISE SPECIFIED,
DIMENSIONS ARE IN MILLIMETERS

TITLE
MAIN ENCLOSURE ASSEMBLY

DO NOT SCALE DRAWING

BREAK ALL SHARP EDGES AND

REMOVE BURRS
THIRD ANGLE PROJECTION

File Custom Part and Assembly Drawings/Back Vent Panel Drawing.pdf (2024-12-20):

2
1

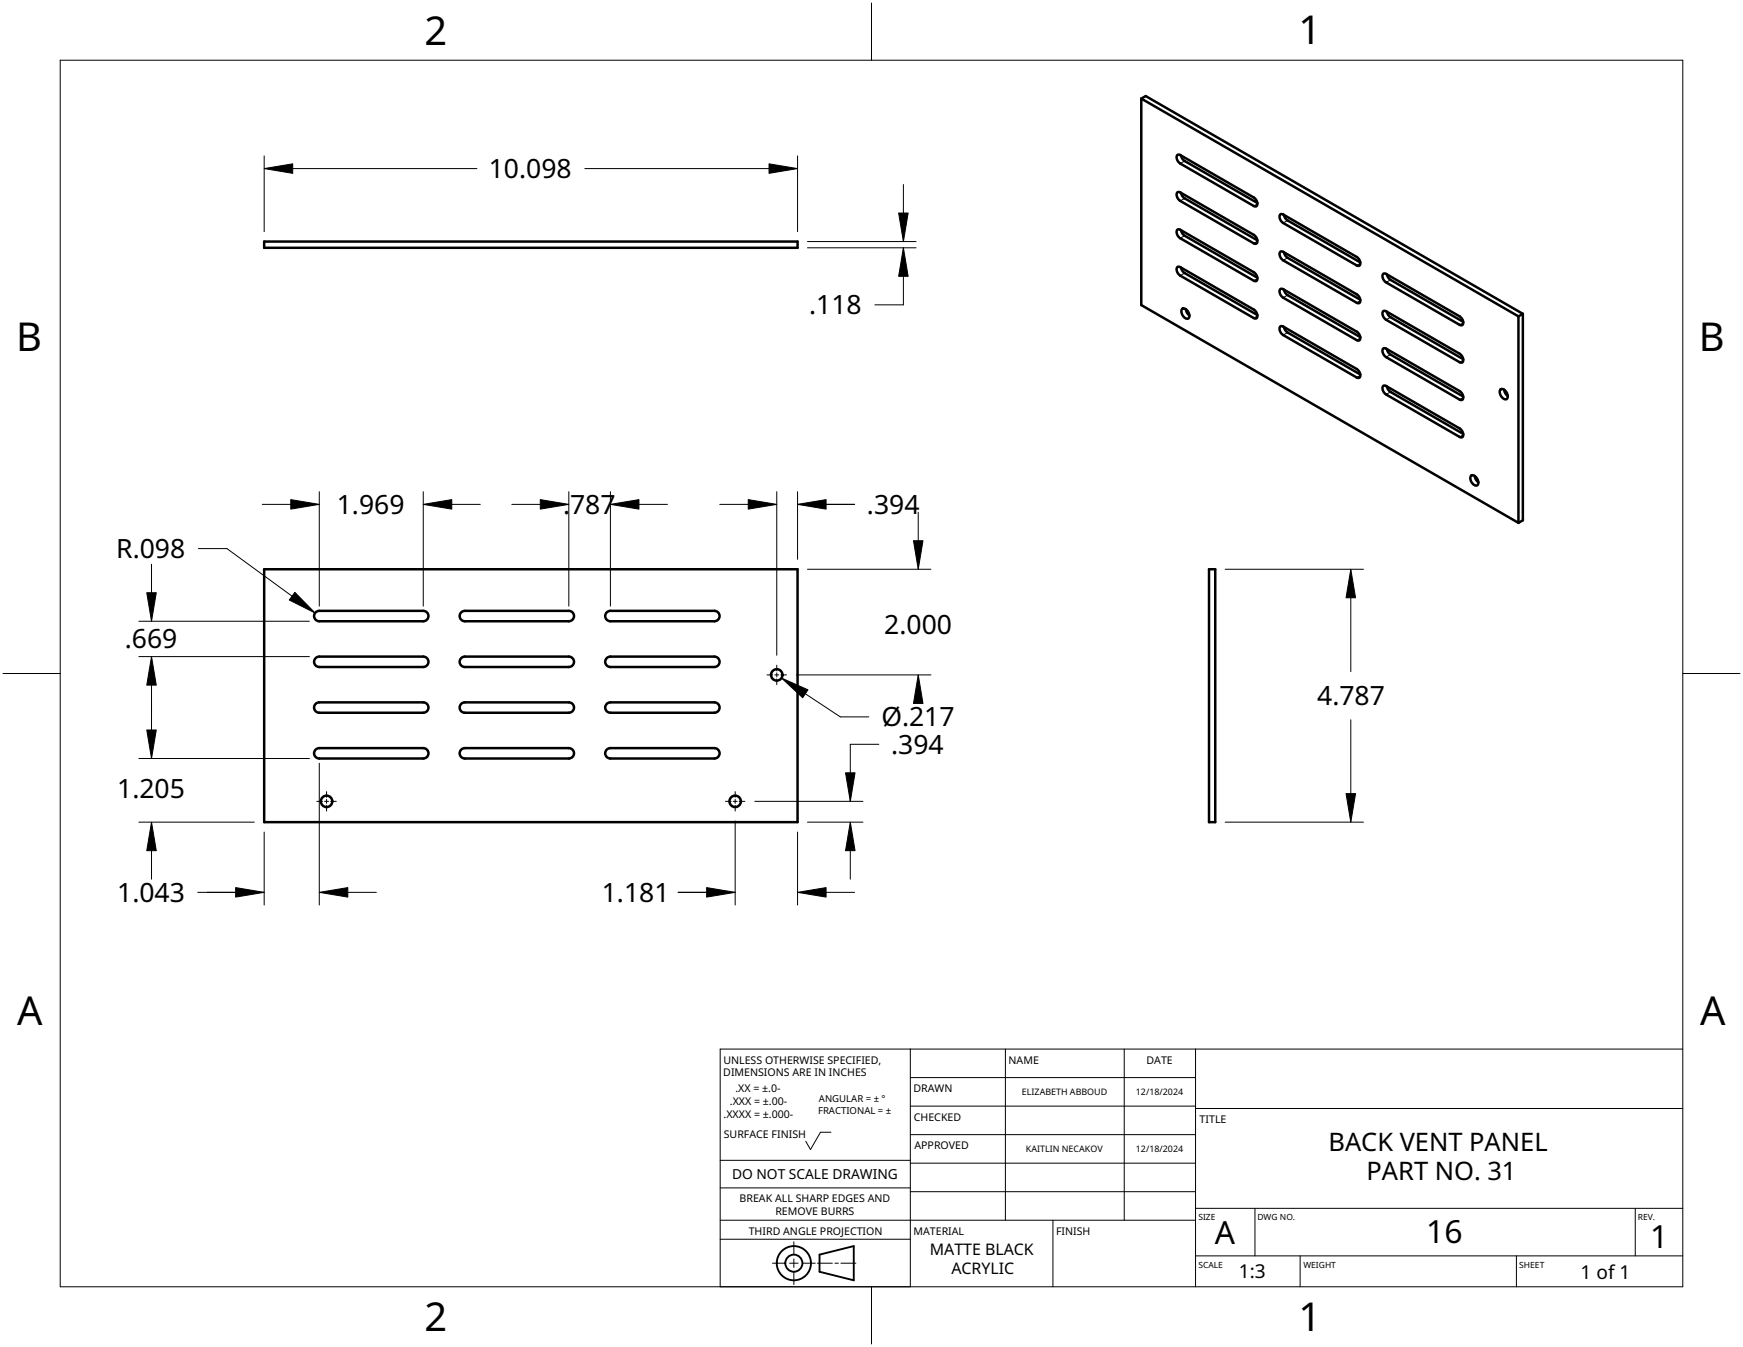
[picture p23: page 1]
MATERIAL MATTE BLACK ACRYLIC; FINISH; SIZE A; DWG NO.; REV.; 1 SCALE; WEIGHT; SHEET

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

DRAWN | ELIZABETH ABBOUD | 12/18/2024

CHECKED | | | TITLE BACK VENT PANEL PART NO. 31

APPROVED | KAITLIN NECAKOV | 12/18/2024

DO NOT SCALE DRAWING

BREAK ALL SHARP EDGES AND

REMOVE BURRS
THIRD ANGLE PROJECTION

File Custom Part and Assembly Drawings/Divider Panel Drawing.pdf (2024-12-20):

2
1

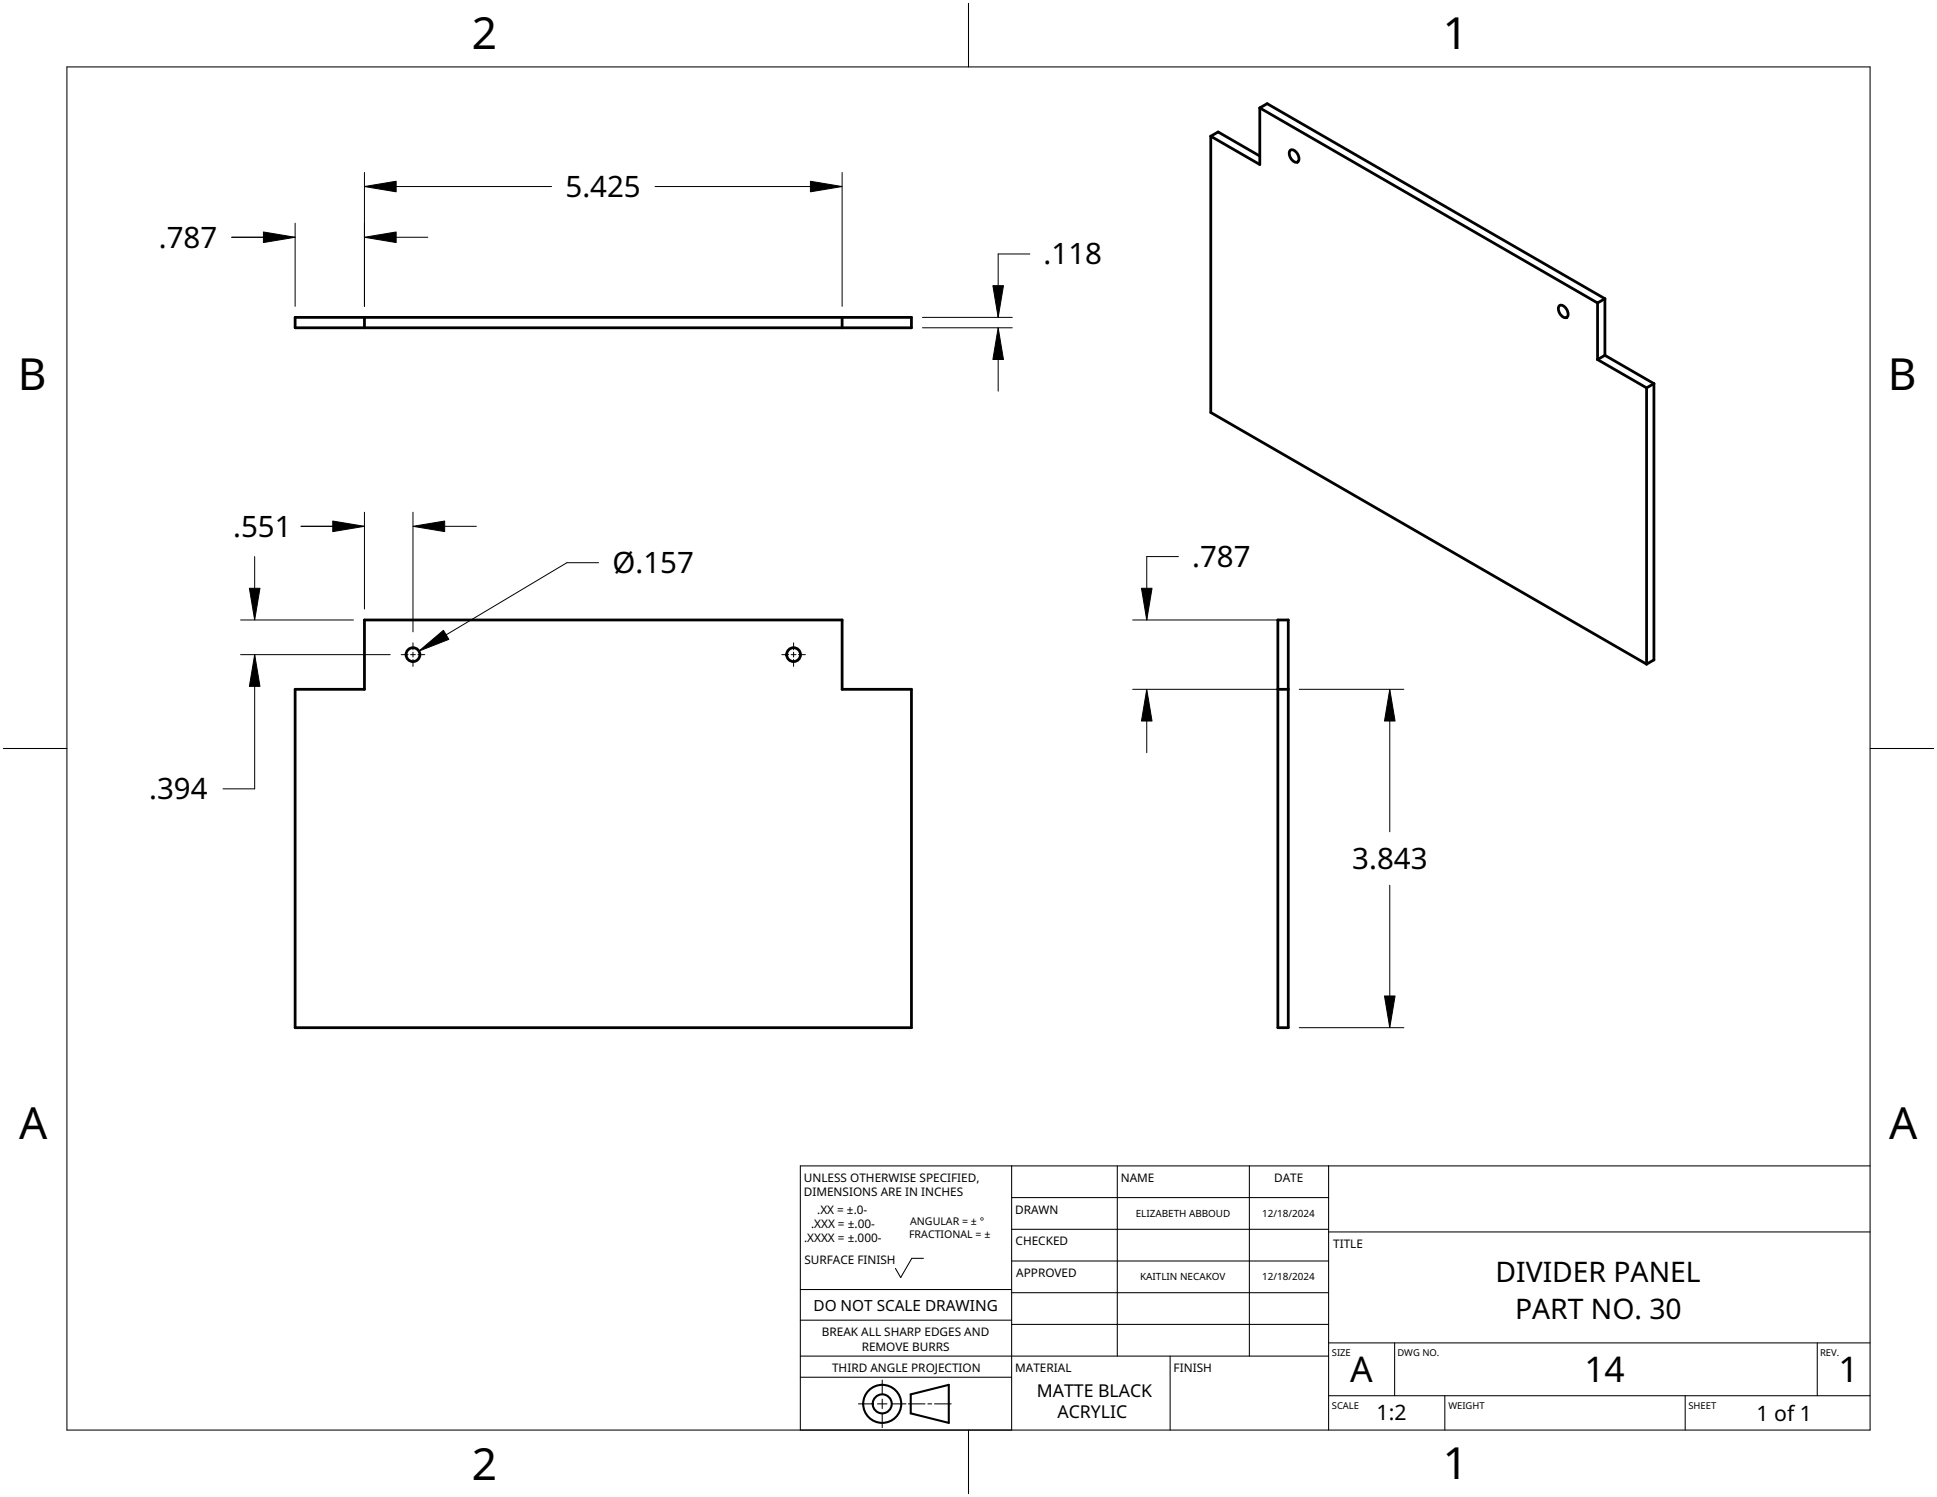
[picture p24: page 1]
MATERIAL MATTE BLACK ACRYLIC; FINISH

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

DRAWN | ELIZABETH ABBOUD | 12/18/2024

CHECKED | | | TITLE DIVIDER PANEL PART NO. 30

APPROVED | KAITLIN NECAKOV | 12/18/2024

DO NOT SCALE DRAWING

BREAK ALL SHARP EDGES AND

REMOVE BURRS
THIRD ANGLE PROJECTION

SIZE A | DWG NO. 14 | REV. 1

SCALE 1:2 | WEIGHT | SHEET 1 of 1

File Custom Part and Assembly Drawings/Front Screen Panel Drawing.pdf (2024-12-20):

2
1

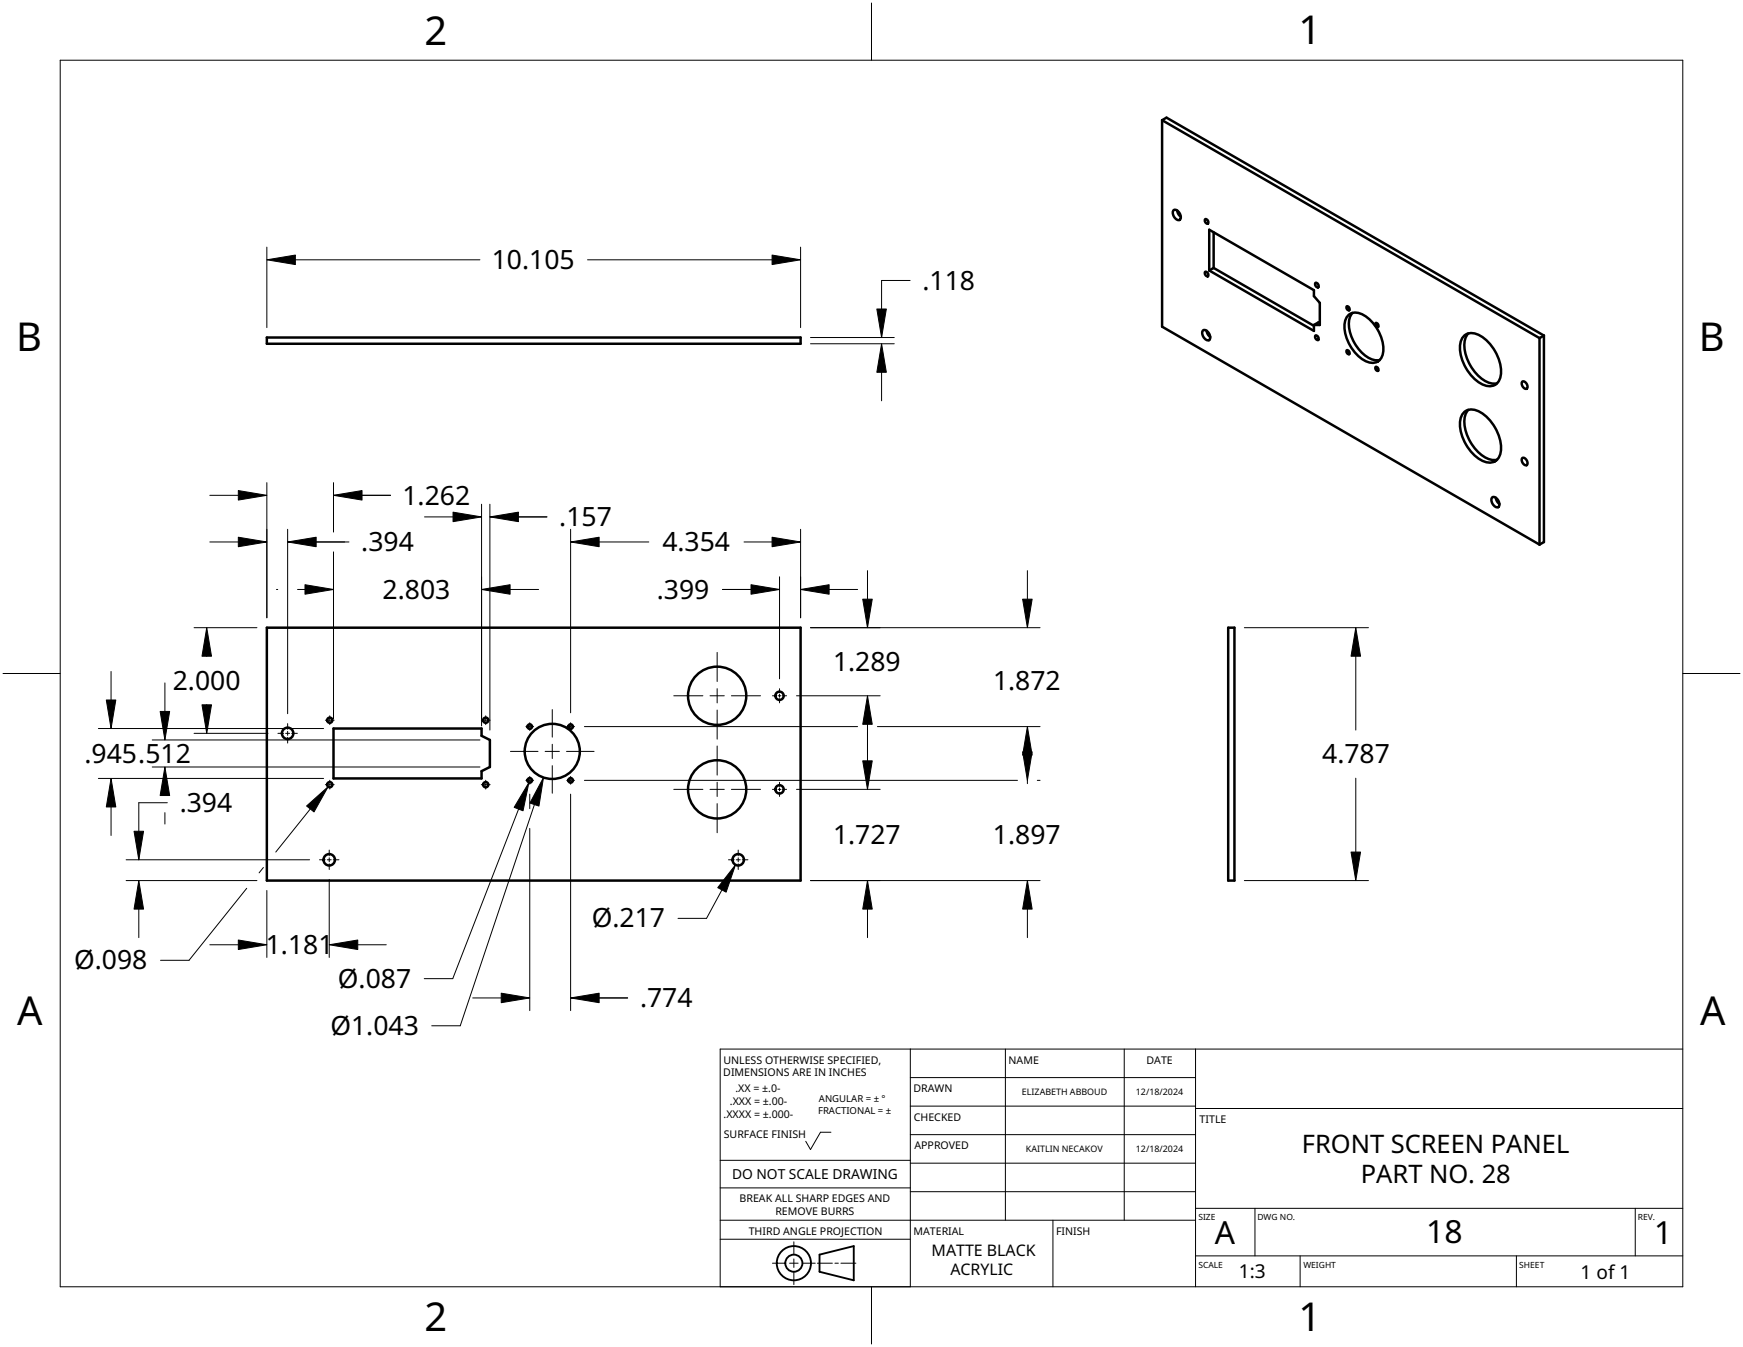
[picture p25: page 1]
MATERIAL MATTE BLACK ACRYLIC; FINISH

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

DRAWN | ELIZABETH ABBOUD | 12/18/2024

CHECKED | | | TITLE FRONT SCREEN PANEL PART NO. 28

APPROVED | KAITLIN NECAKOV | 12/18/2024

DO NOT SCALE DRAWING

BREAK ALL SHARP EDGES AND

REMOVE BURRS
THIRD ANGLE PROJECTION

SIZE A | DWG NO. 18 | REV. 1

SCALE 1:3 | WEIGHT | SHEET 1 of 1

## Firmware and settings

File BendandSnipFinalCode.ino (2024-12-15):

#include <Wire.h>
#include <LiquidCrystal_I2C.h>
#include <Stepper.h>

LiquidCrystal_I2C lcd(0x27, 16, 2);

// Pin definitions for the joystick
const int joyX = A0;  // X-axis (horizontal)
const int joyY = A1;  // Y-axis (vertical)
const int joySwitch = 22; // Digital pin for joystick button


// Variables for zero calibration
int zeroX = 0;
int zeroY = 0;

// Variables for wire length and wire count
int wireLength = 5; // Start within the range for wire length (5-130 mm)
int wireCount = 1;  // Start within the range for wire count (1-240)

// Threshold to detect movement
const int threshold = 300;

// Timing variables for continuous increment/decrement
unsigned long lastActionTime = 0;
const unsigned long actionInterval = 200; // Time in milliseconds between increments/decrements

// Mode flag: true for setting wire length, false for wire count
bool settingWireLength = true;

// Define the number of steps per revolution for your stepper motor
const int stepsPerRevolution = 200; // Adjust this based on your motor's specification

// Define pins for power and stop buttons
const int startbutton = 18;
const int stopbutton = 19;

// Create instances of the Stepper class for each motor
Stepper myStepper1(stepsPerRevolution, 6, 7, 8, 9);
Stepper myStepper2(stepsPerRevolution, 10, 11, 12, 13);
Stepper myStepper3(stepsPerRevolution, 2, 3, 4, 5);

// Conversion factor: Steps per millimeter
const int stepsPerMillimeter = 7; //(7.11 steps / 1 mm)

// Variables for user input of desired length and number of wires
int desiredLength = 0;
int stepsToMove = 0;
int desireCount = 0;
// Variable to control Voltage spikes
int skipstart = 0;


// State variables for button controls
volatile byte isMotorOn = false; // Tracks whether the motor is running
volatile byte startButtonPressed = false;
volatile byte stopButtonPressed = false;
volatile int myStepper2Position = 0; // Tracks position relative to zero (in steps)

void setup() {
  myStepper1.setSpeed(200);    // Set speed (in RPM) for myStepper1
  myStepper2.setSpeed(200);    // Set speed (in RPM) for myStepper2
  myStepper3.setSpeed(200);    // Set speed (in RPM) for myStepper3
  Serial.begin(9600);          // Initialize serial communication

  lcd.init();
  lcd.backlight();

  pinMode(joySwitch, INPUT_PULLUP); // Set joystick switch pin as input with pull-up resistor
  pinMode(startbutton, INPUT_PULLUP); // Set button pins as inputs with pull-up resistors
  pinMode(stopbutton, INPUT_PULLUP);

  // Attach interrupts for start and stop buttons
  attachInterrupt(digitalPinToInterrupt(startbutton), togglestart, FALLING);
  attachInterrupt(digitalPinToInterrupt(stopbutton), togglestop, FALLING);

  // Calibrate zero positions
  zeroX = analogRead(joyX);
  zeroY = analogRead(joyY);


  // Initialize display
  lcd.clear();
  updateDisplay();
}

void loop() {
  // Read raw joystick positions
  int xVal = analogRead(joyX);
  int yVal = analogRead(joyY);
  int switchState = digitalRead(joySwitch); // Read joystick switch state

  // Toggle mode when the switch is pressed
  if (switchState == LOW) { // Switch is active when LOW
    settingWireLength = !settingWireLength; // Toggle mode
    delay(300); // Debounce delay
    updateDisplay(); // Update display to reflect mode change
  }

  // Calculate differences from zero
  int deltaX = abs(xVal - zeroX);
  int deltaY = abs(yVal - zeroY);

  // Check if the joystick is moved beyond the threshold
  if (abs(deltaX) > threshold || abs(deltaY) > threshold) {
    if (millis() - lastActionTime > actionInterval) {
      if (deltaY > threshold) {
        // Increment based on the current mode
        if (settingWireLength) {
          wireLength++;
          if (wireLength > 130) wireLength = 5; // Wrap wire length
        } else {
          wireCount++;
          if (wireCount > 240) wireCount = 1; // Wrap wire count
        }
      } else if (deltaY < -threshold) {
        // Decrement based on the current mode
        if (settingWireLength) {
          wireLength--;
          if (wireLength < 5) wireLength = 130; // Wrap wire length
        } else {
          wireCount--;
          if (wireCount < 1) wireCount = 240; // Wrap wire count
        }
      }

      // Update last action time
      lastActionTime = millis();

      // Update the display
      Serial.print(settingWireLength ? "Wire Length: " : "Wire Count: ");
      Serial.println(settingWireLength ? wireLength : wireCount);
      updateDisplay();
    }
  } else {
    lastActionTime = 0; // Reset the timer if the joystick is in the neutral position
  }

  // Check if power button was pressed
  if ((startButtonPressed) && (skipstart != 0)) {
    startButtonPressed = false; // Reset flag
    isMotorOn = !isMotorOn;     // Toggle motor state
    if (isMotorOn) {
      Serial.println("Motor sequence started!");
    }
  }
  if ((startButtonPressed) && (skipstart == 0)) {
    skipstart++;
    startButtonPressed = false; // Reset flag
    Serial.println("False start");
    delay(200);
  }



  // Execute the motor sequence only if the start button has been pressed and skipstart != 0 
  if (isMotorOn) {
    for (int w = 1; w <= wireCount; w++) {
      // 1. Move myStepper1 first (wireLength * stepsPerMillimeter steps)
      Serial.println("Moving Stepper 1");
      moveStepper(myStepper1, 75, false);

      // 2. Move myStepper2 down (458 steps)
      Serial.println("Moving Stepper 2 down");
      moveStepper(myStepper2, 503, false);  // Move down

      // 3. Move myStepper2 up (458 steps)
      Serial.println("Moving Stepper 2 up");
      moveStepper(myStepper2, 503, true); // Move up

      // 4. Move myStepper1 back (100 steps)
      Serial.println("Moving Stepper 1");
      moveStepper(myStepper1, 100, true);

      // 5. Move myStepper1 forward
      Serial.println("Moving Stepper 1");
      moveStepper(myStepper1, wireLength * stepsPerMillimeter + 100 +75, false);

      // 6. Move myStepper2 down  (458 steps)
      Serial.println("Moving Stepper 2 down");
      moveStepper(myStepper2, 503, true);  // Move down

      // 7. Move myStepper2 up (458 steps)
      Serial.println("Moving Stepper 2 up");
      moveStepper(myStepper2, 503, fasle); // Move up

      // 8. Move myStepper1 back
      Serial.println("Moving Stepper 1");
      moveStepper(myStepper1, wireLength * stepsPerMillimeter, true);

      // 9. Spin myStepper3 forward
      Serial.println("Moving Stepper 3");
      moveStepper(myStepper3, 200, false);

      // 10. Move myStepper1 forward
      Serial.println("Moving Stepper 1");
      moveStepper(myStepper1, 100, false);

      // 11. Spin myStepper3 forward
      Serial.println("Moving Stepper 3");
      moveStepper(myStepper3, 200, false);

      // 12. Move myStepper2 to cut
      Serial.println("Moving Stepper 2 down");
      moveStepper(myStepper2, 650, true); // Move forward

      // 13. Move myStepper2 to go up after cut
      Serial.println("Moving Stepper 2 up");
      moveStepper(myStepper2, 650, false); // Move backward

      // 14. Move myStepper1 forward
      Serial.println("Moving Stepper 1");
      moveStepper(myStepper1, 200, true);

      // 15. Move myStepper1 forward
      Serial.println("Moving Stepper 1");
      moveStepper(myStepper1, 200, false);

    // Adjust after 30 runs
      if (w >= 30) {
        Serial.println("Moving Stepper 2 down");
        moveStepper(myStepper2, 15, false); // Move up
        Serial.println("Motors adjusted after 30 runs.");
      } else {
        Serial.print("Motor sequence completed ");
        Serial.print(w);
        Serial.println(" times.");
      }
      if (stopButtonPressed) {
        stopButtonPressed = false; // Reset flag
        Serial.println("Motor sequence stopped!");
        break; 
  }
    }
      isMotorOn = false;
      Serial.println("Moving Stepper 2 up");
      Serial.println("Motor sequence completed after desired amount is reached.");

    }
  }

// Function to update the LCD display
void updateDisplay() {
  lcd.clear();
  // Display wire length on the top line
  lcd.setCursor(0, 0);
  lcd.print("Wire (mm): ");
  lcd.print(wireLength);

  // Display wire count on the bottom line
  lcd.setCursor(0, 1);
  lcd.print("# Wires: ");
  lcd.print(wireCount);

  // Highlight current mode
  if (settingWireLength) {
    lcd.setCursor(15, 0); // Add indicator to the top line
    lcd.print("*");
  } else {
    lcd.setCursor(15, 1); // Add indicator to the bottom line
    lcd.print("*");
  }
}

// Function to move a stepper motor a specific number of steps in a given direction
void moveStepper(Stepper &stepper, int steps, bool forward) {
  int stepDirection = forward ? 1 : -1;
  for (int i = 0; i < steps; i++) {
    stepper.step(stepDirection);
    delay(5); // Short delay for smoother movement

    // Update position tracking for myStepper2
    if (&stepper == &myStepper2) {
      myStepper2Position += forward ? 1 : -1;
    }
  }
}

void togglestop() {
  // Debounce delay in the ISR
  static unsigned long lastInterruptTime = 0;
  unsigned long interruptTime = millis();
  if (interruptTime - lastInterruptTime > 500) { // Debounce interval (200 ms)
    stopButtonPressed = true;
    isMotorOn = false;        // Stop motor sequence
    Serial.println("stop button pressed");
  }
}

void togglestart() {
  static unsigned long lastInterruptTime = 0;
  unsigned long interruptTime = millis();
  if (interruptTime - lastInterruptTime > 500) {
    startButtonPressed = true;
    Serial.println("start button pressed");
  }
  lastInterruptTime = interruptTime;
}

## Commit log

2024-12-15 Add files via upload
    Final Code for Bend & Snip. This code controls the entire system (motor sequences, buttons, and screen).
2024-12-20 Create 3D Print STL Files
2024-12-20 Create Laser Cutting DXF Files
